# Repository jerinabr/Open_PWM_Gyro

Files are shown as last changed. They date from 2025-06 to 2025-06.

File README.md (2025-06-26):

# Open_PWM_Gyro
## Description
6-channel PWM gyro for fixed wing RC planes. Meant to be connected to an ELRS RX or other RX that outputs CRSF serial data.

### Layer Stackup
This is a 4-layer board with the following stackup:
1. Signal + Power
2. Ground
3. Ground
4. Signal + Power

Both ground layers are solid ground pours and aren't shown in the images section below

### Features
- USB-C for device firmware upgrade and configuration
- SWD header for device programming and debugging
- 2-color status LED (red, blue) controlled by the MCU
- Boot switch to allow the device to enter the bootloader on power-up
- 6-axis IMU (3-axis accelerometer, 3-axis gyroscope)
- Pin header for servo/ESC connections with one 3-pin group for serial data input from the RX

### Firmware
Firmware for this gyro can be found [in this repo](https://github.com/jerinabr/Open_PWM_Gyro_Firmware)

## BOM
| Reference | Qty | Value | Footprint | DigiKey Part # |
| --- | --- | --- | --- | --- |
| C1,C5,C6,C7,C8,C9,C12 | 7 | 0.1u | Capacitor_SMD:C_0402_1005Metric_Pad0.74x0.62mm_HandSolder | 1276-6720-1-ND |
| C2,C4 | 2 | 1u | Capacitor_SMD:C_0402_1005Metric_Pad0.74x0.62mm_HandSolder | 1276-1445-1-ND |
| C3 | 1 | 22u | Capacitor_SMD:CP_Elec_4x5.4 | 732-8413-1-ND |
| C10,C11 | 2 | 10p | Capacitor_SMD:C_0402_1005Metric_Pad0.74x0.62mm_HandSolder | 311-1014-1-ND |
| D1 | 1 | PMEG2005CT,215 | Package_TO_SOT_SMD:SOT-23 | 1727-5188-2-ND |
| J1 | 1 | USB_C_Receptacle_USB2.0_16P | Connector_USB:USB_C_Receptacle_GCT_USB4105-xx-A_16P_TopMnt_Horizontal | 2073-USB4105-GF-ATR-ND |
| J2 | 1 | Conn_01x21 | Connector_PinHeader_2.54mm_Custom:PinHeader_3x07_P2.54mm_Vertical | TSW-107-26-F-T-ND |
| LED1 | 1 | LED_Dual_AKKA | LED_SMD_Custom:LED_APHBM2012QBDSURKC | 754-1506-1-ND |
| MT1 | 1 | ICM-42605 | Package_LGA_Custom:XDCR_ICM-42605 | 1428-1152-1-ND |
| R1,R2 | 2 | 5k1 | Resistor_SMD:R_0402_1005Metric_Pad0.72x0.64mm_HandSolder | 13-RC0402FR-135K1LCT-ND |
| R3,R5 | 2 | 10k | Resistor_SMD:R_0402_1005Metric_Pad0.72x0.64mm_HandSolder | 311-10KJRCT-ND |
| R4 | 1 | 68 | Resistor_SMD:R_0402_1005Metric_Pad0.72x0.64mm_HandSolder | 311-68.0LRCT-ND |
| SW1 | 1 | SW_SPST | Button_Switch_SMD_Custom:R-667995_MIT | 2508-R-667995TR-ND |
| SWD1 | 1 | Conn_02x05_Odd_Even | Connector_PinHeader_1.27mm:PinHeader_2x05_P1.27mm_Vertical | S9015E-05-ND |
| U1 | 1 | TCR2EF33_LMCT | Package_TO_SOT_SMD_Custom:SOT-25 SMV_TOS | TCR2EF33LM(CTTR-ND |
| U2 | 1 | STM32G431KBTx | Package_QFP:LQFP-32_7x7mm_P0.8mm | 497-19470-ND |
| Y1 | 1 | Crystal_GND24 | Crystal_Custom:Crystal_SMD_ECS_ECX_2236-4Pin_2.5x2.0mm | 50-ECS-160-10-36-CKM-TR3TR-ND |

> [!NOTE]
> J2 is a 3x7 2.54mm pitch pin header. This part can be replaced with three 7-pin headers or seven 3-pin headers or some other combination to save cost

## Images
### Schematic
#### Page 1: Power + Connectors
Schematic Page 1: Power + Connectors
#### Page 2: MCU + IMU
Schematic Page 2: MCU + IMU
### PCB
#### Top Layer
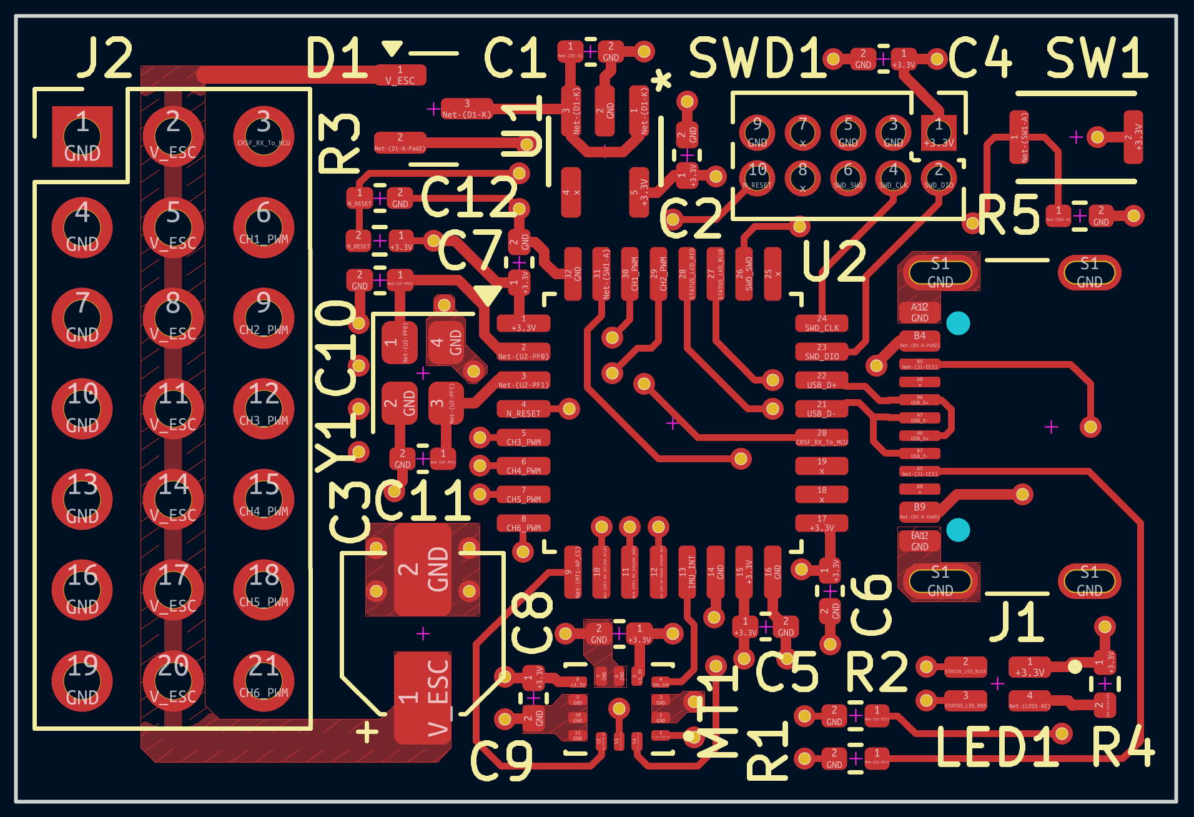
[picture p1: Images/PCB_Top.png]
PCB Top Layer

#### Bottom Layer
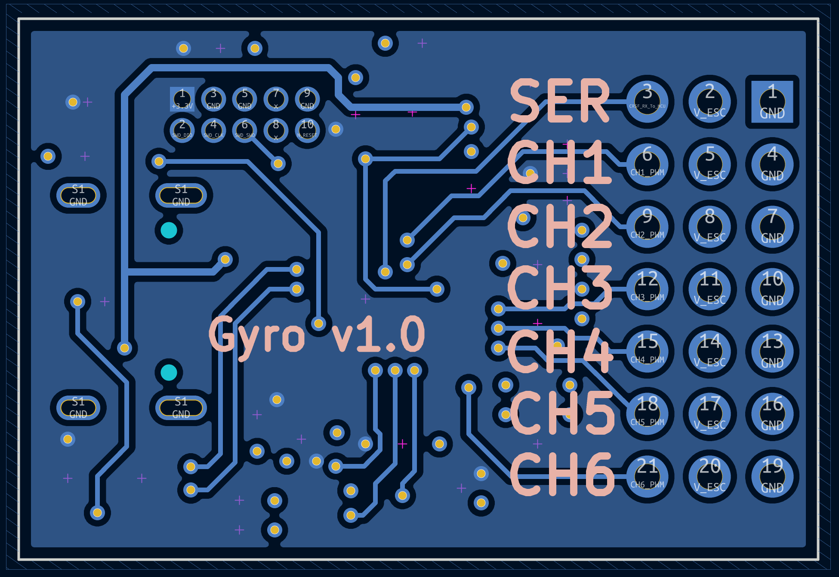
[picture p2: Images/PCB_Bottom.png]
PCB Bottom Layer

#### Top + Bottom Layer
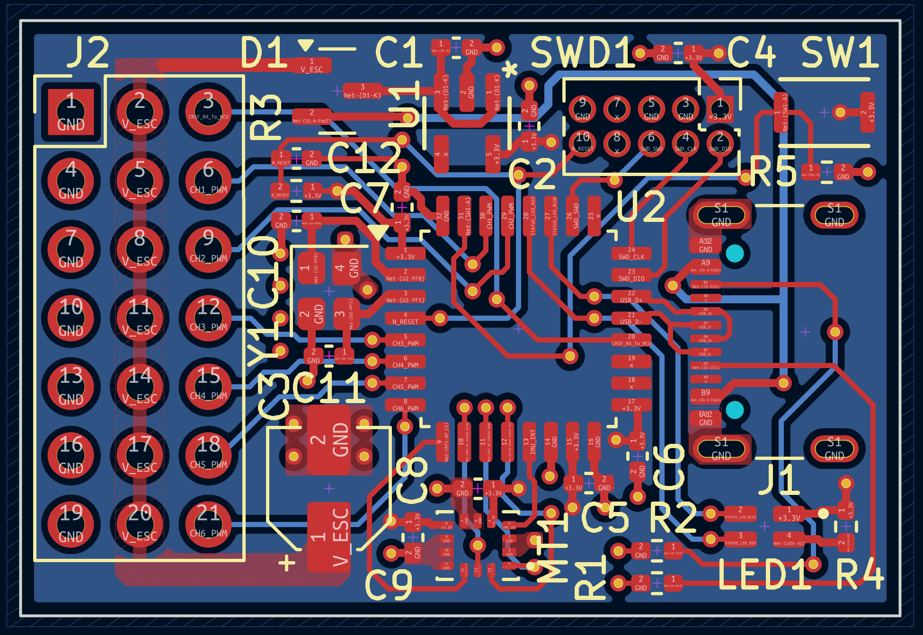
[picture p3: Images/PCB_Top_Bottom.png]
PCB Top + Bottom Layer

### 3D View
#### Top
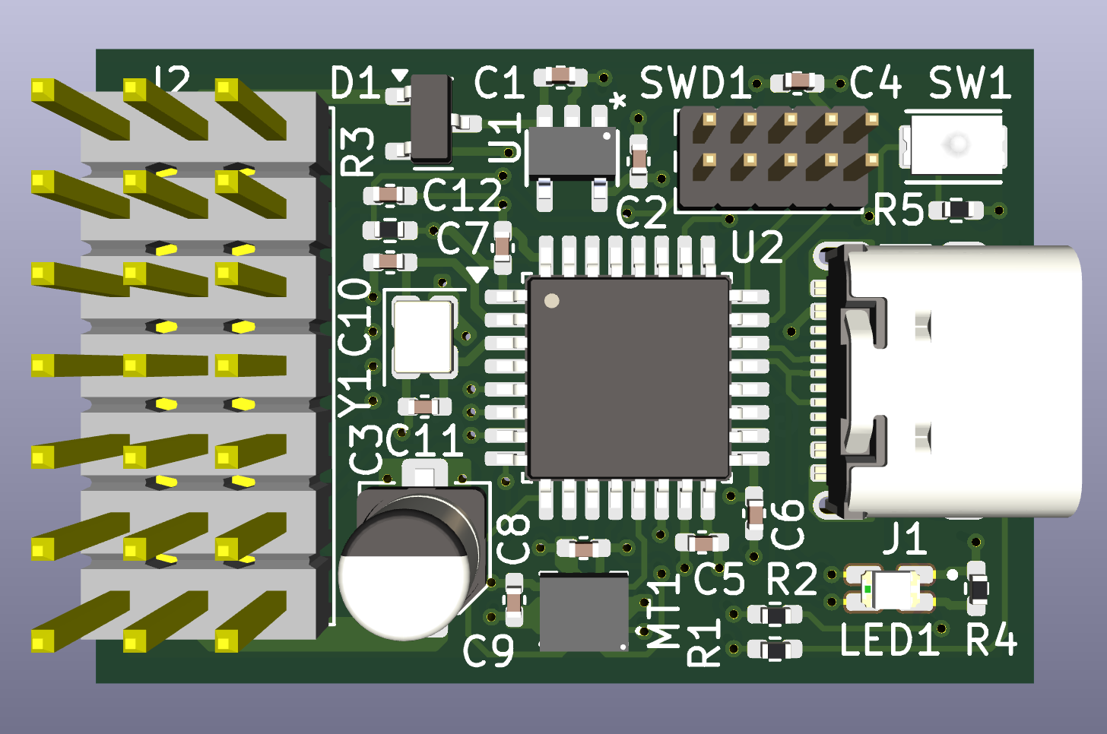
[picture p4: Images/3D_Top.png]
3D Top View

#### Bottom
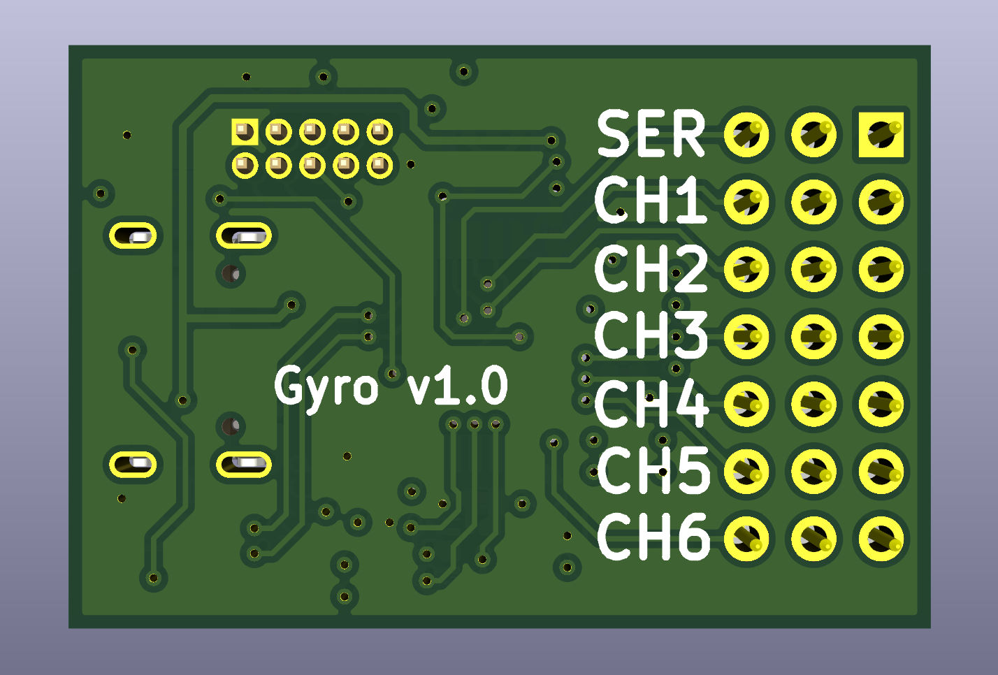
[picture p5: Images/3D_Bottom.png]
3D Bottom View


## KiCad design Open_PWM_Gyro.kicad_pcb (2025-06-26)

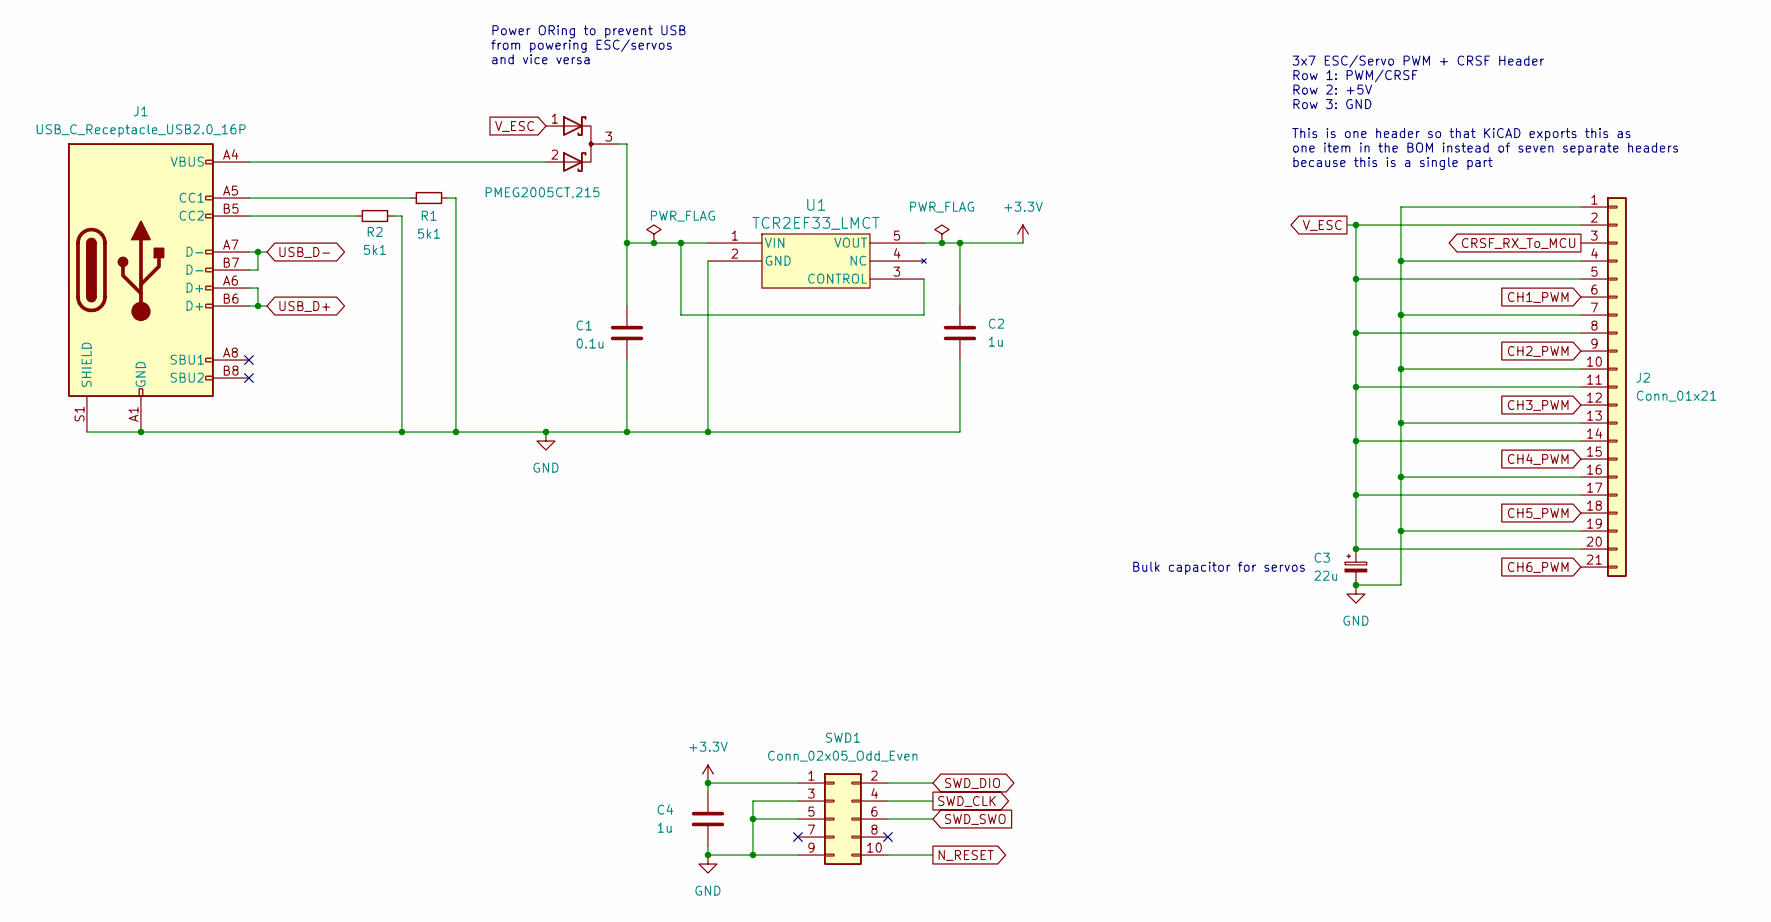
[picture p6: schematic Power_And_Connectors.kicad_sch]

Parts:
C1: 0.1u; C_0402_1005Metric_Pad0.74x0.62mm_HandSolder; Mfg Part # CL05B104KA5NNNC; DigiKey Part # 1276-6720-1-ND
C2, C4: 1u; C_0402_1005Metric_Pad0.74x0.62mm_HandSolder; Mfg Part # CL05A105KA5NQNC; DigiKey Part # 1276-1445-1-ND
C3: 22u; CP_Elec_4x5.4; Mfg Part # 865080340003; DigiKey Part # 732-8413-1-ND
D1: PMEG2005CT,215; SOT-23; Mfg Part # PMEG2005CT,215; DigiKey Part # 1727-5188-2-ND
J1: USB_C_Receptacle_USB2.0_16P; USB_C_Receptacle_GCT_USB4105-xx-A_16P_TopMnt_Horizontal; Mfg Part # USB4105-GF-A; DigiKey Part # 2073-USB4105-GF-ATR-ND
J2: Conn_01x21; PinHeader_3x07_P2.54mm_Vertical; Mfg Part # TSW-107-26-F-T; DigiKey Part # TSW-107-26-F-T-ND
R1, R2: 5k1; R_0402_1005Metric_Pad0.72x0.64mm_HandSolder; Mfg Part # RC0402FR-135K1L; DigiKey Part # 13-RC0402FR-135K1LCT-ND
SWD1: Conn_02x05_Odd_Even; PinHeader_2x05_P1.27mm_Vertical; Mfg Part # GRPB052VWVN-RC; DigiKey Part # S9015E-05-ND
U1: TCR2EF33_LMCT; SOT-25 SMV_TOS; Mfg Part # TCR2EF33,LM(CT; DigiKey Part # TCR2EF33LM(CTTR-ND

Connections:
+3.3V: C2.1, C4.1, SWD1.1, U1.5 (VOUT); also elsewhere on the board
CH1_PWM: J2.6; also elsewhere on the board
CH2_PWM: J2.9; also elsewhere on the board
CH3_PWM: J2.12; also elsewhere on the board
CH4_PWM: J2.15; also elsewhere on the board
CH5_PWM: J2.18; also elsewhere on the board
CH6_PWM: J2.21; also elsewhere on the board
CRSF_RX_To_MCU: J2.3; also elsewhere on the board
GND: C1.2, C2.2, C3.2, C4.2, J1.A1 (GND), J1.A12 (GND), J1.B1 (GND), J1.B12 (GND), J1.S1 (SHIELD), J2.1, J2.4, J2.7, J2.10, J2.13, J2.16, J2.19, R1.2, R2.2, SWD1.3, SWD1.5, SWD1.9, U1.2 (GND); also elsewhere on the board
N_RESET: SWD1.10; also elsewhere on the board
unnamed: D1.2 (A), J1.A4 (VBUS), J1.A9 (VBUS), J1.B4 (VBUS), J1.B9 (VBUS)
unnamed: C1.1, D1.3 (K), U1.1 (VIN), U1.3 (CONTROL)
unnamed: J1.A5 (CC1), R1.1
unnamed: J1.B5 (CC2), R2.1
SWD_CLK: SWD1.4; also elsewhere on the board
SWD_DIO: SWD1.2; also elsewhere on the board
SWD_SWO: SWD1.6; also elsewhere on the board
USB_D+: J1.A6 (D+), J1.B6 (D+); also elsewhere on the board
USB_D-: J1.A7 (D-), J1.B7 (D-); also elsewhere on the board
V_ESC: C3.1, D1.1 (A), J2.2, J2.5, J2.8, J2.11, J2.14, J2.17, J2.20

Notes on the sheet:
Bulk capacitor for servos
Power ORing to prevent USB from powering ESC/servos and vice versa
3x7 ESC/Servo PWM + CRSF Header Row 1: PWM/CRSF Row 2: +5V Row 3: GND This is one header so that KiCAD exports this as one item in the BOM instead of seven separate headers because this is a single part

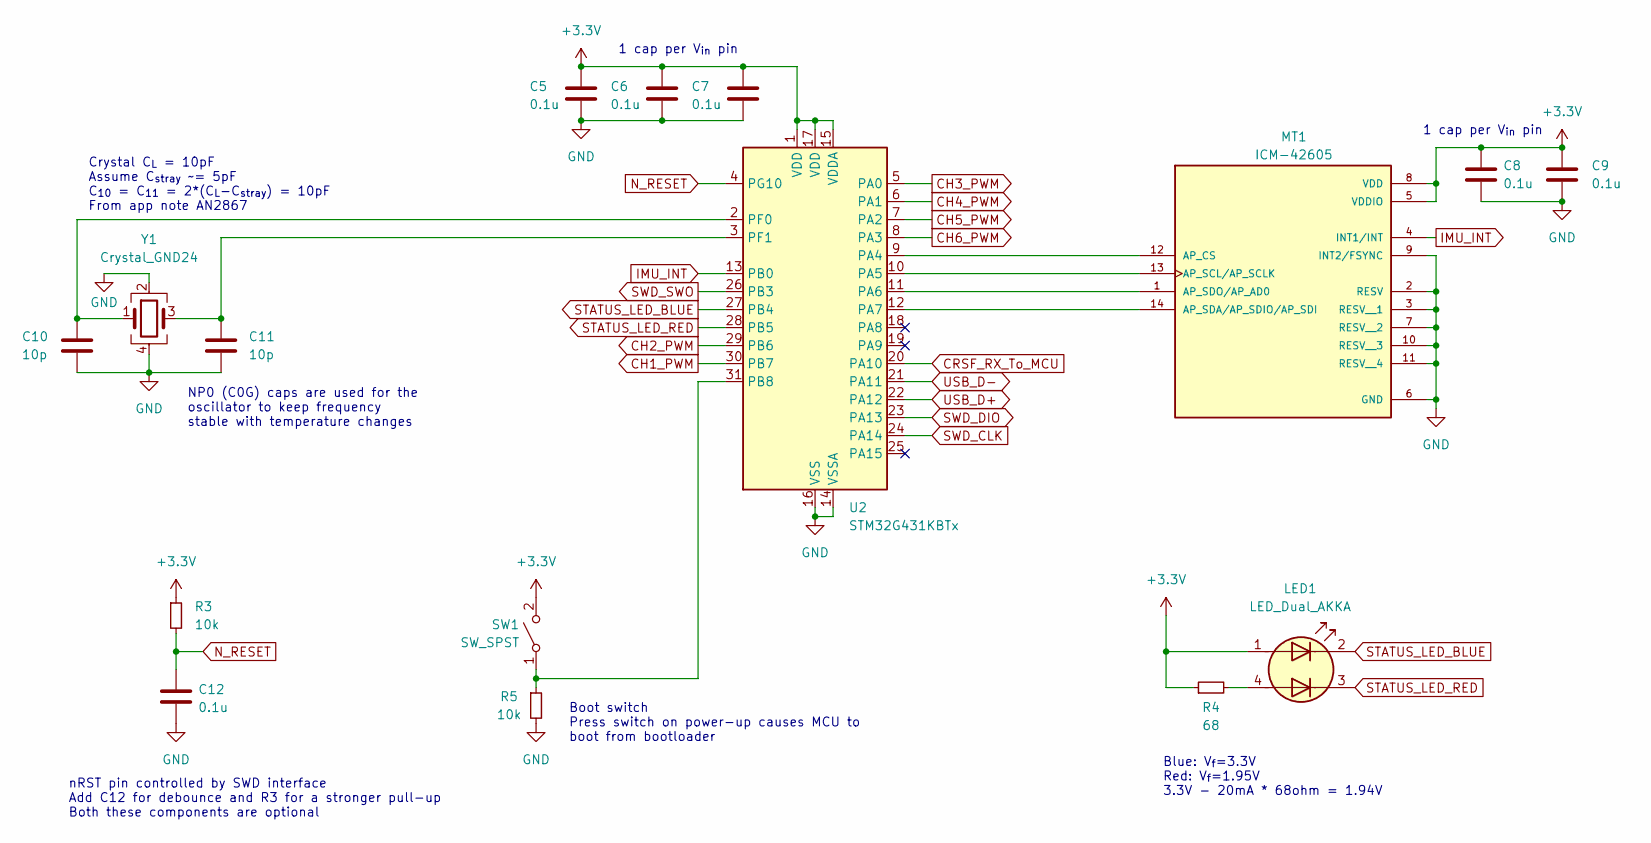
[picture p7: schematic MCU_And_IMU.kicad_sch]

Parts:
C5, C6, C7, C8, C9, C12: 0.1u; C_0402_1005Metric_Pad0.74x0.62mm_HandSolder; Mfg Part # CL05B104KA5NNNC; DigiKey Part # 1276-6720-1-ND
C10, C11: 10p; C_0402_1005Metric_Pad0.74x0.62mm_HandSolder; Mfg Part # CC0402JRNPO9BN100; DigiKey Part # 311-1014-1-ND
LED1: LED_Dual_AKKA; LED_APHBM2012QBDSURKC; Mfg Part # APHBM2012QBDSURKC; DigiKey Part # 754-1506-1-ND
MT1: ICM-42605; XDCR_ICM-42605; PARTREV 1.7; DigiKey Part # 1428-1152-1-ND
R3, R5: 10k; R_0402_1005Metric_Pad0.72x0.64mm_HandSolder; Mfg Part # RC0402JR-0710KL; DigiKey Part # 311-10KJRCT-ND
R4: 68; R_0402_1005Metric_Pad0.72x0.64mm_HandSolder; Mfg Part # RC0402FR-0768RL; DigiKey Part # 311-68.0LRCT-ND
SW1: SW_SPST; R-667995_MIT; Mfg Part # R-667995; DigiKey Part # 2508-R-667995TR-ND
U2: STM32G431KBTx; LQFP-32_7x7mm_P0.8mm; Mfg Part # STM32G431KBT6; DigiKey Part # 497-19470-ND
Y1: Crystal_GND24; Crystal_SMD_ECS_ECX_2236-4Pin_2.5x2.0mm; Mfg Part # ECS-160-10-36-CKM-TR3; DigiKey Part # 50-ECS-160-10-36-CKM-TR3TR-ND

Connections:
+3.3V: C5.1, C6.1, C7.1, C8.1, C9.1, LED1.1 (A1), MT1.5 (VDDIO), MT1.8 (VDD), R3.1, R4.1, SW1.2 (B), U2.1 (VDD), U2.15 (VDDA), U2.17 (VDD); also elsewhere on the board
CH1_PWM: U2.30 (PB7); also elsewhere on the board
CH2_PWM: U2.29 (PB6); also elsewhere on the board
CH3_PWM: U2.5 (PA0); also elsewhere on the board
CH4_PWM: U2.6 (PA1); also elsewhere on the board
CH5_PWM: U2.7 (PA2); also elsewhere on the board
CH6_PWM: U2.8 (PA3); also elsewhere on the board
CRSF_RX_To_MCU: U2.20 (PA10); also elsewhere on the board
GND: C5.2, C6.2, C7.2, C8.2, C9.2, C10.2, C11.2, C12.2, MT1.2 (RESV), MT1.3 (RESV__1), MT1.6 (GND), MT1.7 (RESV__2), MT1.9 (INT2/FSYNC), MT1.10 (RESV__3), MT1.11 (RESV__4), R5.2, U2.14 (VSSA), U2.16 (VSS), U2.32 (VSS), Y1.2, Y1.4; also elsewhere on the board
IMU_INT: MT1.4 (INT1/INT), U2.13 (PB0)
N_RESET: C12.1, R3.2, U2.4 (PG10); also elsewhere on the board
unnamed: LED1.4 (A2), R4.2
unnamed: MT1.12 (AP_CS), U2.9 (PA4)
unnamed: MT1.13 (AP_SCL/AP_SCLK), U2.10 (PA5)
unnamed: MT1.14 (AP_SDA/AP_SDIO/AP_SDI), U2.12 (PA7)
unnamed: MT1.1 (AP_SDO/AP_AD0), U2.11 (PA6)
unnamed: R5.1, SW1.1 (A), U2.31 (PB8)
unnamed: C10.1, U2.2 (PF0), Y1.1
unnamed: C11.1, U2.3 (PF1), Y1.3
STATUS_LED_BLUE: LED1.2 (K1), U2.27 (PB4)
STATUS_LED_RED: LED1.3 (K2), U2.28 (PB5)
SWD_CLK: U2.24 (PA14); also elsewhere on the board
SWD_DIO: U2.23 (PA13); also elsewhere on the board
SWD_SWO: U2.26 (PB3); also elsewhere on the board
USB_D+: U2.22 (PA12); also elsewhere on the board
USB_D-: U2.21 (PA11); also elsewhere on the board

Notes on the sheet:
NP0 (C0G) caps are used for the oscillator to keep frequency stable with temperature changes
Blue: V_{f}=3.3V Red: V_{f}=1.95V 3.3V - 20mA * 68ohm = 1.94V
1 cap per V_{in} pin
Boot switch Press switch on power-up causes MCU to boot from bootloader
nRST pin controlled by SWD interface Add C12 for debounce and R3 for a stronger pull-up Both these components are optional
Crystal C_{L} = 10pF Assume C_{stray} ~= 5pF C_{10} = C_{11} = 2*(C_{L}-C_{stray}) = 10pF From app note AN2867

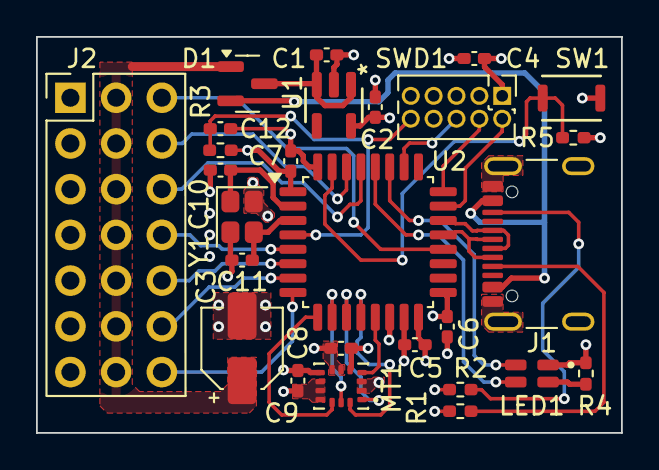
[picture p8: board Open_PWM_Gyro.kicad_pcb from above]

Board: 4 copper layers, 32.5 x 22.0 mm, 27 parts (0 on the bottom side), 31 nets.

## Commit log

2025-05-26 Add main components to schematic
    [CRSF_PWM_Gyro.kicad_sch]
2025-05-29 Move hardware files into hardware folder
    [CRSF_PWM_Gyro.kicad_pcb, CRSF_PWM_Gyro.kicad_sch]
2025-05-31 Pick different MCU and add USB C connector
    [CRSF_PWM_Gyro.kicad_sch]
2025-06-04 Add CRSF header and replace MCU with KB variant
    [CRSF_PWM_Gyro.kicad_sch]
2025-06-06 Separate schematic into pages
    [CRSF_PWM_Gyro.kicad_sch, MCU_And_IMU.kicad_sch, Power_And_Connectors.kicad_sch]
2025-06-07 Update footprints and add all PNs
    [CRSF_PWM_Gyro.kicad_pcb, CRSF_PWM_Gyro.kicad_sch, MCU_And_IMU.kicad_sch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]
2025-06-08 Swap PWM channels and initial PCB layout
    [CRSF_PWM_Gyro.kicad_pcb, MCU_And_IMU.kicad_sch, Power_And_Connectors.kicad_sch]
2025-06-12 Update components and layout
    [CRSF_PWM_Gyro.kicad_pcb, MCU_And_IMU.kicad_sch, Power_And_Connectors.kicad_sch]
2025-06-14 Made footprint updates
    [CRSF_PWM_Gyro.kicad_pcb, Power_And_Connectors.kicad_sch]
2025-06-15 Complete initial routing
    [CRSF_PWM_Gyro.kicad_pcb, MCU_And_IMU.kicad_sch, Power_And_Connectors.kicad_sch]
2025-06-15 Add images and BOM CSV
    [CRSF_PWM_Gyro.csv, Power_And_Connectors.kicad_sch]
2025-06-15 Make minor routing changes
    [CRSF_PWM_Gyro.kicad_pcb]
2025-06-16 Add other fields to BOM
    [CRSF_PWM_Gyro.kicad_pcb, MCU_And_IMU.kicad_sch, Power_And_Connectors.kicad_sch]
2025-06-22 Clean up routing and layout
    [CRSF_PWM_Gyro.csv, CRSF_PWM_Gyro.kicad_pcb, MCU_And_IMU.kicad_sch]
2025-06-22 Move some silkscreen text
    [CRSF_PWM_Gyro.kicad_pcb]
2025-06-23 Add gerbers and change file structure
    [CRSF_PWM_Gyro-B_Cu.gbr, CRSF_PWM_Gyro-B_Mask.gbr, CRSF_PWM_Gyro-B_Paste.gbr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]
2025-06-26 Rename project and update gerbers
    [Open_PWM_Gyro-B_Cu.gbr, Open_PWM_Gyro-B_Mask.gbr, Open_PWM_Gyro-B_Paste.gbr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]
2025-06-26 Rename bom file and add to bom folder
    [bom.csv]
